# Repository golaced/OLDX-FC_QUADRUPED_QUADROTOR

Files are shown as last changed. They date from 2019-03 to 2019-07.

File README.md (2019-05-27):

# 1 OLDX-MocoMoco四足机器人开发平台项目  
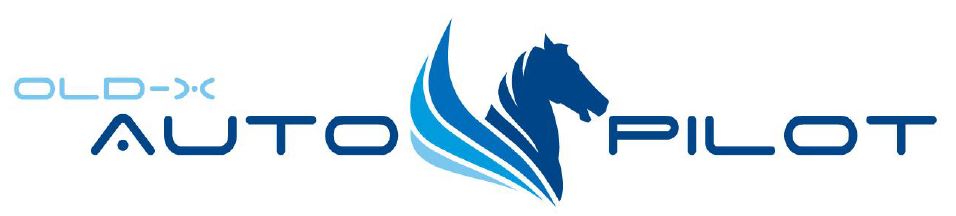
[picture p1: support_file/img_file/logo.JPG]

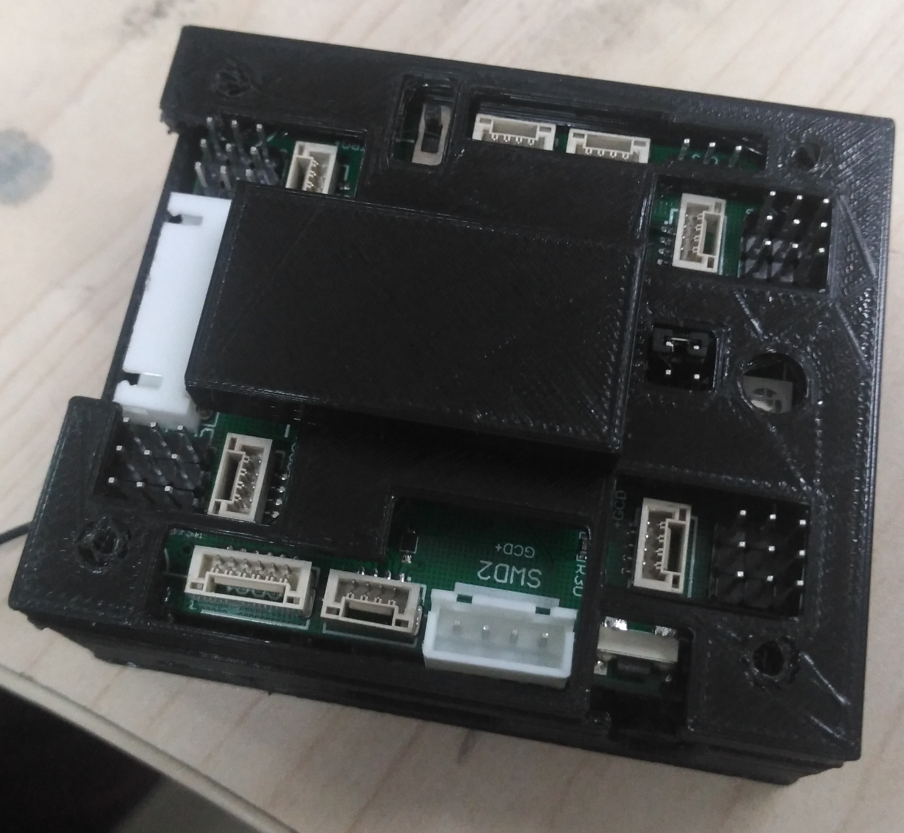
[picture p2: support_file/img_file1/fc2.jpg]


  ____OLDX-MocoMoco四足机器人（OLDX-MocoMoco Quadruped）是目前国内首个真正意义上的开源足式机器人二次开发平台，团队已经开发了一套完整的免费开源
  项目OLDX-FC，随着近年来波士顿动力公司不断推出的足式机器人引起了国内外许多爱好者的关注，也出现了许多电子发烧友自己开发的足式机器人，但
  不同于四轴飞行器仅采用无刷电机和机架就能进行开发，而足式机器人本身结构复杂特别是伺服驱动部分可以独立作为一个学科进行研究，因此造成了
  虽然有许多不错的足式机器人项目但是由于项目成本或者编程语言不为国内环境所熟悉的原因而阻碍了它们的推广或开源。团队4年前就开始研发的六
  足机器人具有丰富的机器人，通过将其与所开发的飞控项目二次结合推出了MocoMoco四足机器人开发平台，囊括机器人结构、步态算法和SLAM无人驾驶
  等多个足式机器人核心技术内容。项目遵循GPL协议，能对DEMO内相关源码进行修改和二次开发。<br><br>

**相关资料** 
机器人测试视频更新地址：https://www.bilibili.com/video/av46405055 <br>
为方便程序单独下载目前各版本固件从这下载：https://github.com/golaced/MocoMoco_Software<br>
机器人校准视频教程：https://www.bilibili.com/video/av51603154<br>
<br>
**-搭建该项目的方式-**

方式|说明|发货周期
-------------|-------------|-------------
整机购买(**推荐**)|从官方淘宝店购买碳素机架+已经加工好的控制器(不包含舵机)|最长半个月
机架打印+控制器购买|自行加工项目文件免费提供的3D打印机架 +从官方购买控制器+自己购买舵机|最长1周
机架打印+控制器制版加工|自行加工3D打印机架+自行制作、焊接控制器+自己购买舵机|控制器(4层板)+IMU+下载器转接+供电模块

**-开源程序与VMC机器人库-**

方式|说明|开源模式
-------------|-------------|-------------
(**VMC机器人库**)|支持多种着地反馈、动态步态调节和更稳定的姿态控制能力，需要向官方购买授权码|闭源(目前支持STM32F4系列，且库与芯片ID绑定)
开源程序|支持基础对角步态和姿态控制|开源

代码版本|开源代码说明|闭源VMC库说明
-------------|--------------|-------------
Publish Ver1.0|(1)虚拟模型基础步态<br>  (2)梯度下降姿态解算<br>  (3)NRF射频通讯遥控<br>  (4)UCOS操作系统|(1)虚拟模型+IMU自稳<br>  (2)动态步态+姿态调节
Publish Ver1.1|(1)SDK开发    |(1)SDK开发<br>	(2)自适应步频<br>	(3)平稳速度S函数切换
Publish Ver1.2|(1)梯度下降融合磁场+磁场干扰判断<br> (2)KF气压计高度融合<br>    (3)KF里程计位姿融合<br>    |(1)位置闭环控制+Jerk轨迹规划<br>   (2)跳跃API<br>   (3)SLIP模式<br> 	(4)梯度下降融合磁场+磁场干扰判断<br> (5)KF气压计高度融合<br>  (6)KF里程计位姿融合<br>   
		
官方机架taobao链接：https://item.taobao.com/item.htm?spm=a1z10.1-c.w4004-15110596499.22.6b86242c3mvjW9&id=589551490320
<br>
**-如果该项目对您有帮助请 Star 我们的项目-**<br>
**-如果您愿意分享对该项目的优化和改进请联系golaced@163.com或加入我们的QQ群567423074，加速开源项目的进度-**<br>

<br>
**-由于本人非专业研究四足机器人，该项目只是基于个人学术水平开发并不代表目前足式机器人算法就是这样，请不要过分依赖项目内容或与正规产品对比-**<br>
	
# 2 MocoMoco四足机器人平台介绍

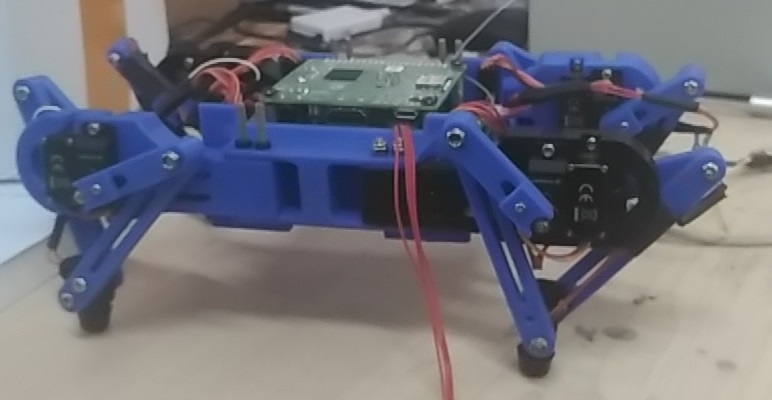
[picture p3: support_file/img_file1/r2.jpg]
 

____MocoMoco四足机器人是一个8自由度足式机器人其借鉴了GhostRobtic推出的Minitature机器人，之所以没有像波士顿动力或其他开发者一样采用
12自由度机器人是因为其在维护难度和成本上都大大提升，而8自由度机器人实际能完美的模拟12自由度单轴的控制特性能快速学习虚拟腿和
虚拟模型相关步态理论，仅损失了部分侧向移动能力。同时对小体积足式机器人来首先与自身移动速度其相比外部环境来说不存绝对意义上狭窄
的区域，能满足绝大部分室内外场景下的可靠移动。<br>
____另外驱动采用固定位置安装的方式使用寿命和维护难度都有较大的优势，适合实验调试中可能出现的损坏等情况。为降低伺服驱动成本将其采用的无刷电机替换为高性能舵机,采用碳板和3D打印件作为主体结构具有安装方便，容易维护的特点，是一个桌面级的四足机器人研发和SLAM算法验证平台。控制器方面采用了目前国内开发群体较多的STM32和树莓派，同时该硬件架构将在后续机器人项目中沿用将首先移植OLDX-FC飞控项目实现真正的
一板多用的目的。电路板硬件方面采用了一体化集成设计采用最小推出的树莓派A3+具有小体积高性能的特点能为后续图像、激光雷达SLAM提供开发可能，
控制板采用STM32F4作为处理器，板载3轴加速度计、3轴陀螺仪、3轴磁力计和气压计采用内减震设计，电路安装孔能完美与树莓派安装同时提供3D打印外壳。
控制板采用外部可更换供电模块供电具有12路PWM输出和4路AD采样，并外扩4路串口兼容正点原子推出的无线调试其方面机器人不同调试。

**控制器硬件参数：**

项目|参数
-------------|-------------
处理器|STM32F405RGT6
处理器性能|32Bit ARM Cortex-M4 168MH
陀螺仪 加速度计|LSM6DS33 
磁力计|LIS3MDL
气压计|MS5611
预留接口|GPS-1 串口-4 AD采样-4 着地开关输入-4
PWM 输出通道| 12通道输出 
供电|5V输入 舵机外部供电  AD传感器3.3/5V供电选择
图像处理器|树莓派A3+  1.4G 4核  带独立供电开关(控制板兼容树莓派全系列可作为外扩IO板安装，但通讯仅采用引脚串口)
遥控方式|2.4G射频 SBUS航模遥控
地面站|QGround   匿名地面站(需要额外OLDX-REMOTE监视器)

**机器人参数：**

项目|参数
-------------|-------------
足式机器人类型|8自由度并联机器人
尺寸|30cm * 20cm *10cm  
全腿长|8cm
重量|600g
供电|7.4V  18650 * 2(3000mah  续航>35 min) 带开关 
步态支持|Tort步态  Fly-Trot步态  波动步态
最大移动速度|0.4m/s
最大转向速度|30度/s
步态周期|>0.35 s
舵机性能|Kpower 12g金属舵机 *8(6V-60度/0.035s  9kg扭矩)
足底传感器|薄膜压力/微动开关(默认无传感器)
控制模式|遥控模式  姿态平衡模式(有/无着地传感器)  驾驶模式  

<br>
**控制器PCB接口说明：**
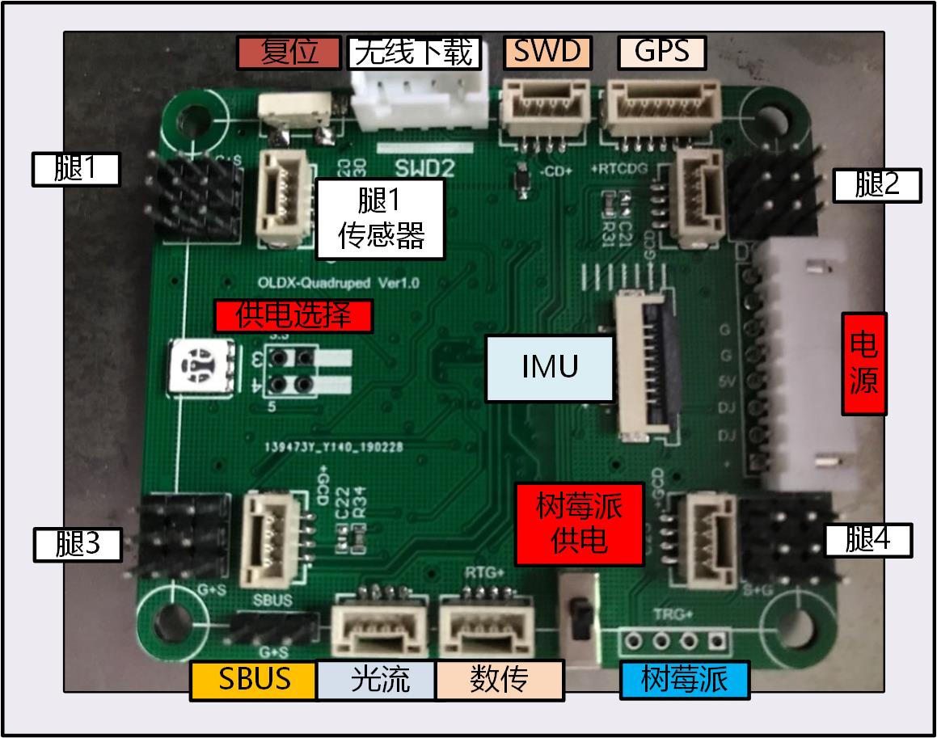
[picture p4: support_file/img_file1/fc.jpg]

<br>

接口|说明(以图片视角)|支持模块
-------------|-------------|-------------
复位|控制器复位按键|
无线下载|从左到右：GND SCK SWD 5V|接正点原子无线调试模块
SWD|从左到右：GND SWD SCK 5V|接Stlink 转接板
GPS|从左到右：5V RX2 TX2 SCL SDA GND|接MINIGPS
足底传感器|从上到下： VCC GND AD1/SCL1 KEY_GROUND1/SDA1|接压力/开关/震动/测距
供电选择|水平跳帽从上到下：3.3V  5V|
SBUS|从左到右：GND 5V Signal|天地飞接收机WBUS  Futaba SBUS接收机
光流|从左到右: RX4 TX4 GND 5V|接光流传感器
数传|从左到右: TX1 RX1 GND 5V|接匿名数传 
树莓派|从左到右：TX3 RX3 GND 5V|树莓派A3
腿1|从左到右：GND VCC PWM   从上到下：外侧舵机  里侧舵机  机械臂/云台|舵机外部供电
电源|从上到下：BEEP 舵机供电使能 GND GND 5V  VCC舵机  VCC舵机 VCC电池|电源模块 

**注：控制器机体为RGB LED方向，上表中仅给出腿1 舵机接口和传感器接口引脚顺序，其余三个腿为镜像对称的结构，
即以腿2为例 从上到下为：外侧舵机  内侧舵机  云台  从左到右为：PWM VCC GND    腿2传感器 从上到下为：
KEY_GROUND2/SDA2  AD2/SCL2  GND  VCC**

# 3 DEMO测试
____该项目免费提供了基础测试的3D打印机架能免费下载自行打印，官方将推出全碳版本的机架请
关注淘宝店后续推出的第三方扩展模块，控制器同时兼任二者各版本机架所需螺丝型号如下：

金属件|数量(3D打印机架)|装配
-------------|-------------|----------
M3*30|8|安装机臂
M2*10|8|安装舵机
M3*5|8|安装腿
M3*10|4|安装足底
M3*15铜柱|4|中心体支撑
M1.4*4|8|固定齿轮
M2.5*3|4|安装电池盒
M2.5*5|8|固定控制器
M2.5铜柱*4|4|控制器支撑

金属件|数量(官方碳素机架)|装配
-------------|-------------|----------
M2*16|8|固定机臂
M2*5|8|安装舵机
M3*5|8|安装腿
M3*10|4|安装足底
M3*32铜柱|4|中心体支撑
M3*4|8|中心体固定
M1.4*4|8|固定齿轮
M2.5*3|4|安装电池盒
M2.5*5|8|固定控制器

## 3.1 控制器组装（树莓派A3）
(1)安装树莓派：<br>
将树莓派按正确方向放入底部外壳中，为避免后续安装相机在该步骤时**最好将树莓派相机对应的CSI排线安装好**，将支撑柱子放入从底部用
M2.5将其与树莓派固定，将CSI排线从外壳对应槽中引出。
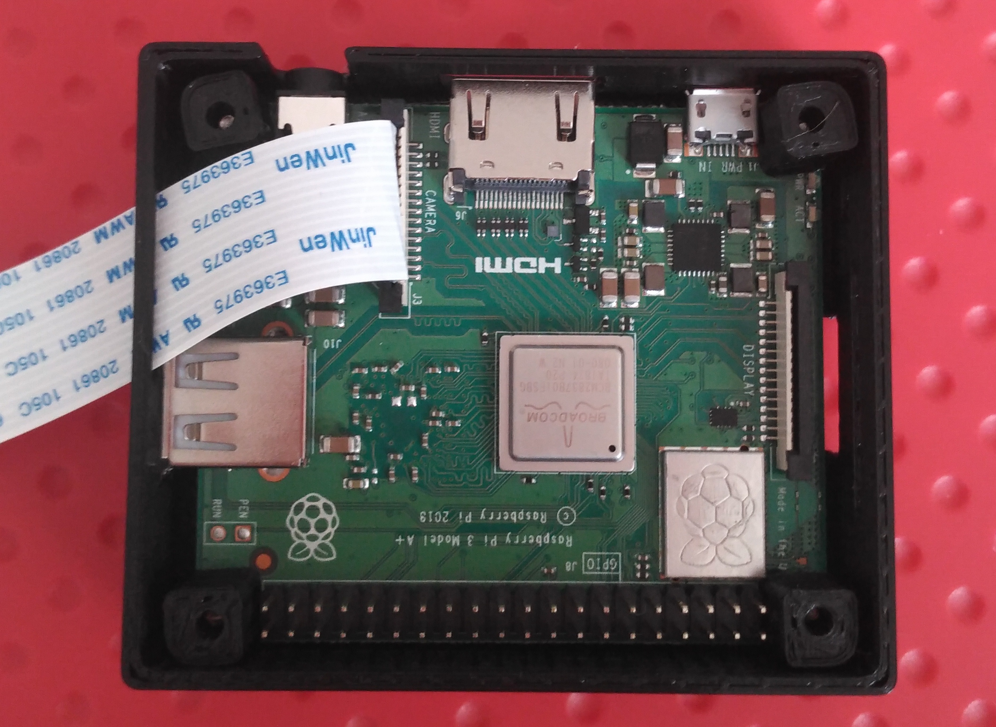
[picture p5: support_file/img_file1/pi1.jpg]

<br>

(2)安装控制器：<br>
将控制器NRF天线从底壳壁上对应圆孔引出，将其按正确朝向安装于树莓派上，注意控制板上只有4P母口其**顶头引脚并非对应树莓派顶头引脚**而且排针为外侧，正确安装应该如下图所示：
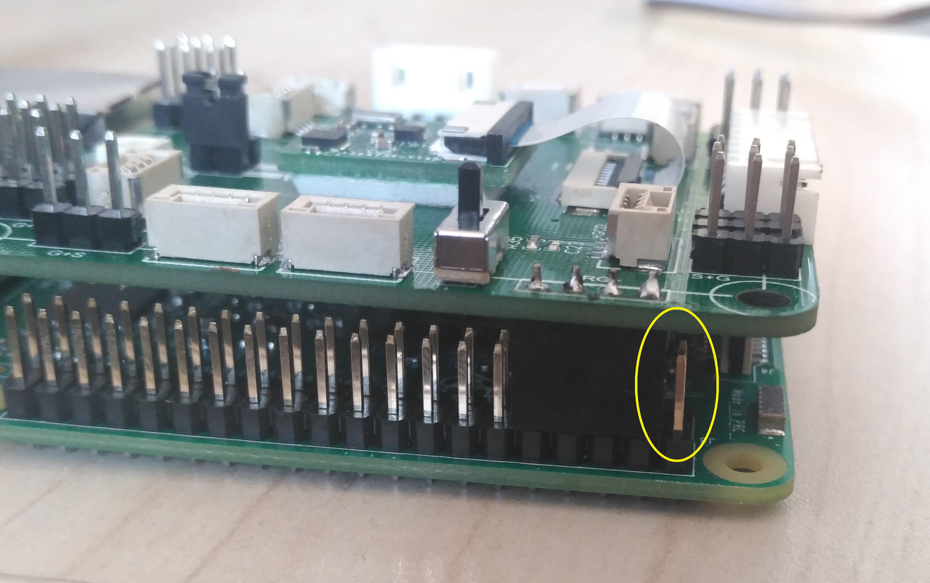
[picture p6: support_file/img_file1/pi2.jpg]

<br>

(3)安装上盖：<br>
将上壳以正确方向安装于控制板上，主要中心空槽应该完整包裹IMU板，完成后同样用M2.5螺丝将上盖固定完成控制器组装。
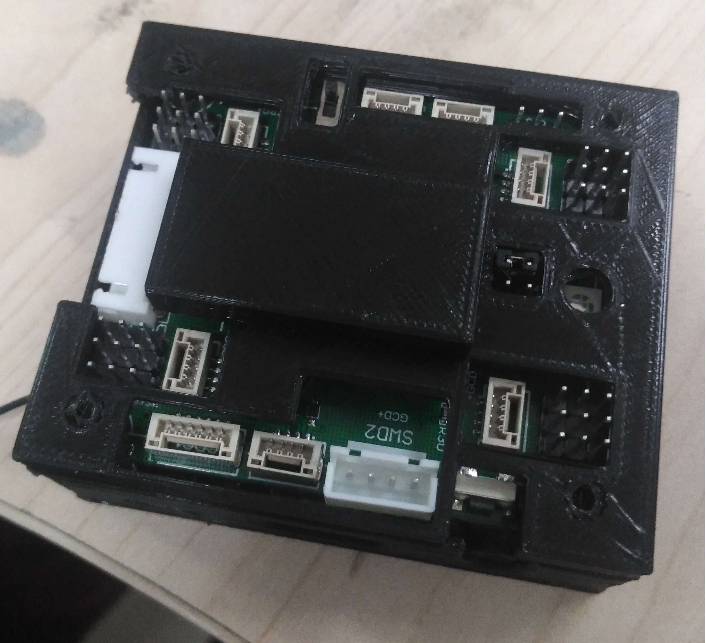
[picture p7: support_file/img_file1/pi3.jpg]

<br>

## 3.2 机器人组装（官方机架）
### 3.2.1 机臂和中心体组装
(1)组装机臂，需要2个机臂碳素片、半圆3D打印件、中心体3D打印支持件，注意机器人机臂需要具有5°的外扩角度，注意上板卡槽为L字，下板卡槽为T字，同时用2mm螺丝加固机臂，结果如下图所示：
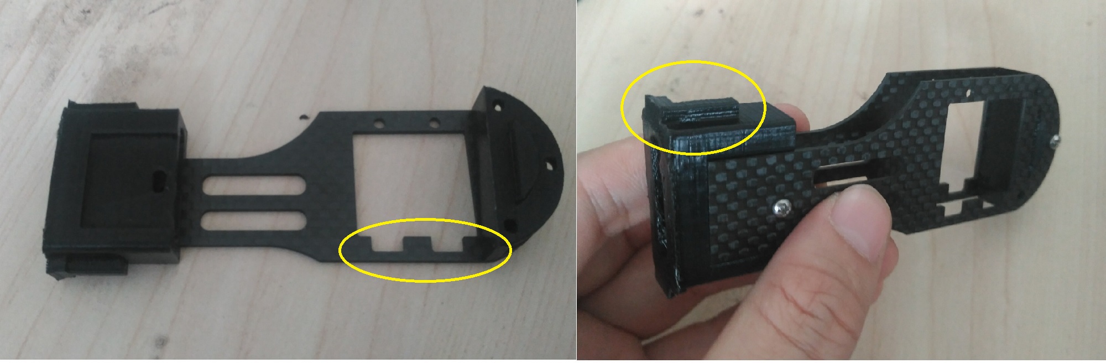
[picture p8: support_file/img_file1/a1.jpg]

<br>
(2)组装中心体，需要上下中心体碳素片、4个M3*32铜柱，首先将铜柱固定在底板上。
<br>
(3)安装机臂，将四个机臂固定在下板卡槽上注意要用5°外扩，结果如下图所示：
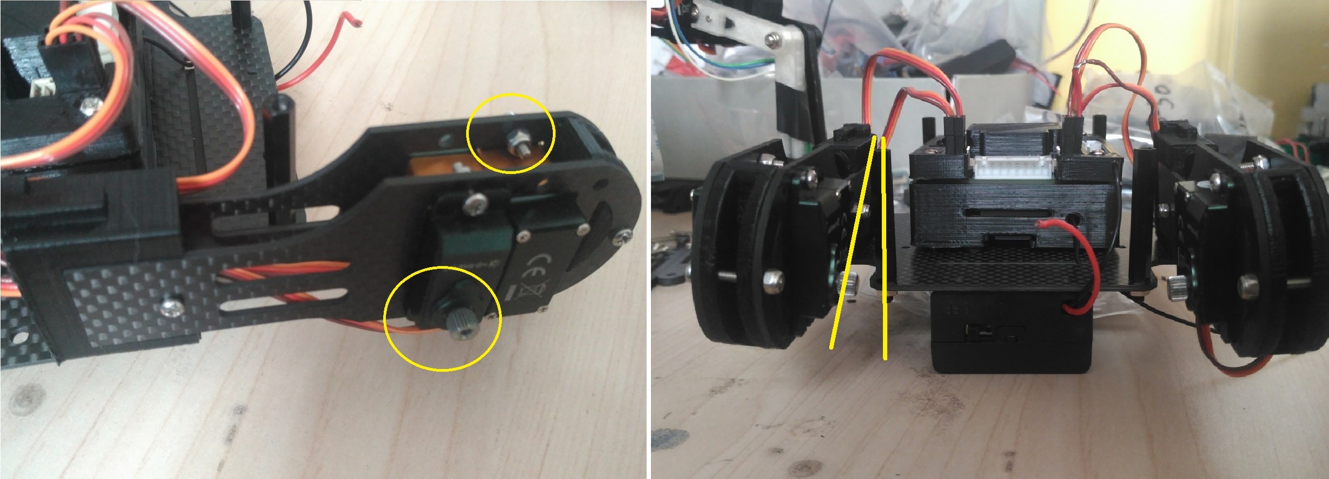
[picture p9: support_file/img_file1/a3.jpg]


### 3.2.2 安装电池仓、控制板和舵机
(1)首先安装电池仓，其安装在中心体底部并且开关方向朝向后方，结果如下图所示：
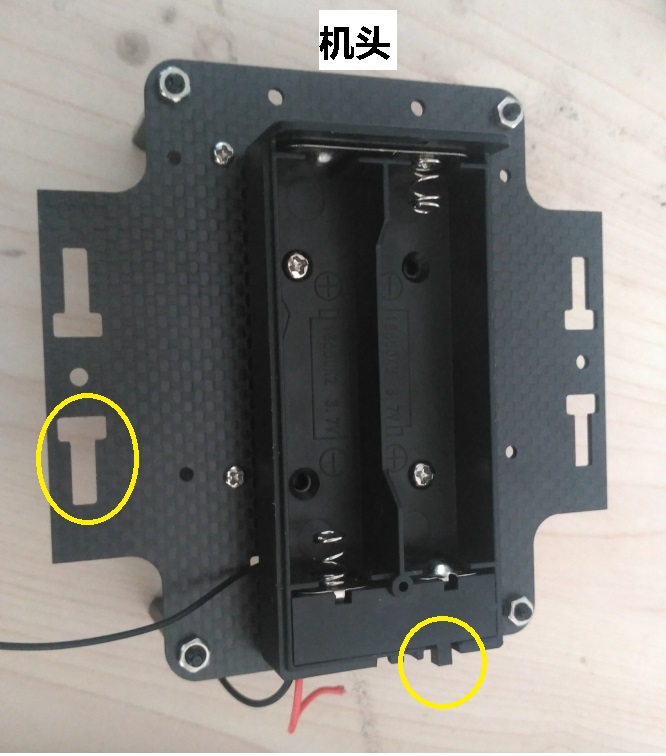
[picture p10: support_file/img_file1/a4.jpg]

<br>
(2)安装舵机，舵机安装采用轴承在下的方式,并且外侧舵机轴承朝向机体内部，内侧舵机轴承超外以保证腿部移动时不会受机体阻碍，用2mm自锁螺丝固定在碳板上，结果如下图所示:
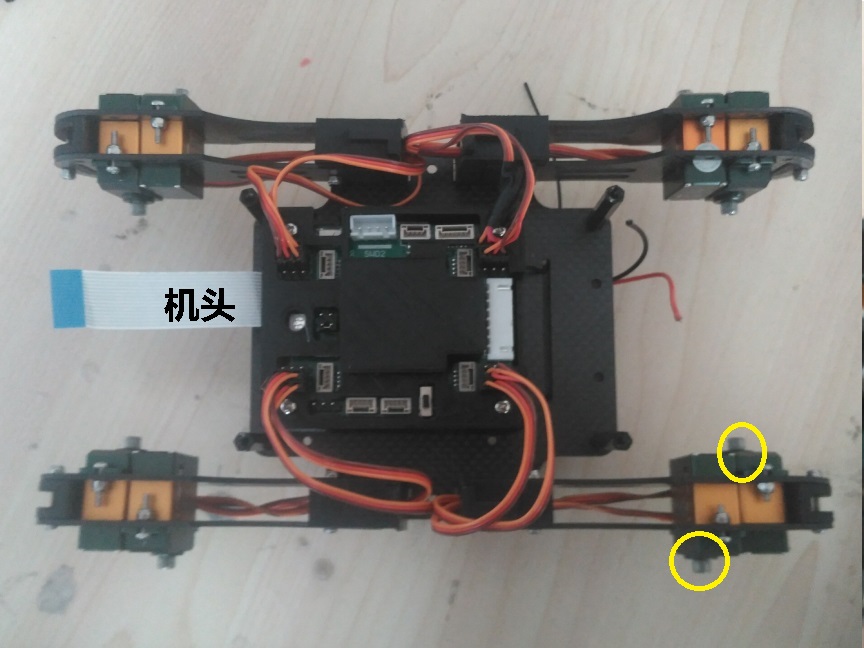
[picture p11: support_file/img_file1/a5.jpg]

<br>
(3)安装控制板，将控制板安装在中心体上方(**推荐用带锁3M胶或魔术贴方便后续SD卡更换**)，主要如没有安装控制器外壳则需要将控制器采用3D打印件垫高以防止电路板底部与碳板和电池仓估计螺丝短路，结果如下图所示:
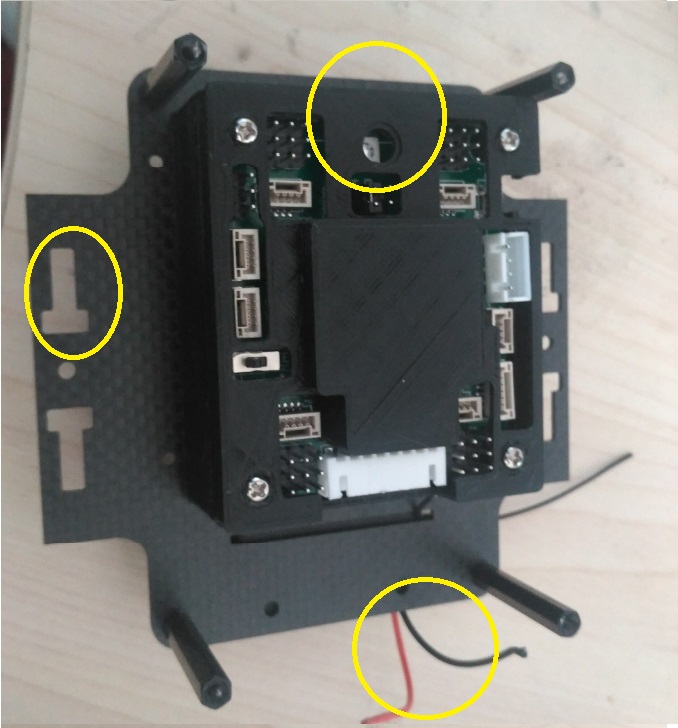
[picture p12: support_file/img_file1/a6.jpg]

<br>
(4)连接舵机线，从机臂内部绕线将舵机线与控制板连接，具体连接顺序参照下标，另外注意PWM引脚朝向机体内部为5V供电即可，具体引脚供电顺序参考PCB IO图：

**舵机接线**
||
-------------|-------------|----------
Sch.PWM3 TIM3_3 [D_LEG] 外舵机1|机体右 |Sch.PWM6 TIM4_2 [D_LEG] 外舵机2
Sch.PWM2 TIM3_2 [X_LEG] 内舵机1| |Sch.PWM5 TIM4_1 [X_LEG] 内舵机2
Sch.PWM1 TIM3_1 NS| |Sch.PWM4 TIM3_4 NS
**机头**||机尾
Sch.PWM7 TIM4_3 NS| |Sch.PWM10 TIM8_1 NS
Sch.PWM8 TIM4_4 [X_LEG] 内舵机3| |Sch.PWM11 TIM8_2 [X_LEG] 内舵机4
Sch.PWM9 TIM1_1 [D_LEG] 外舵机3|机体左 |PSch.WM12 TIM8_3 [D_LEG] 外舵机4

### 3.2.3 连接电子模块和上板
(1)将降压模块与电池仓焊接，注意输入输出关系和正负极，结果如下图所示:
<br>
(2)将降压模块通过XH2.8-8线进行连接，并将降压模块卡入底板后部卡槽，结果如下图所示:
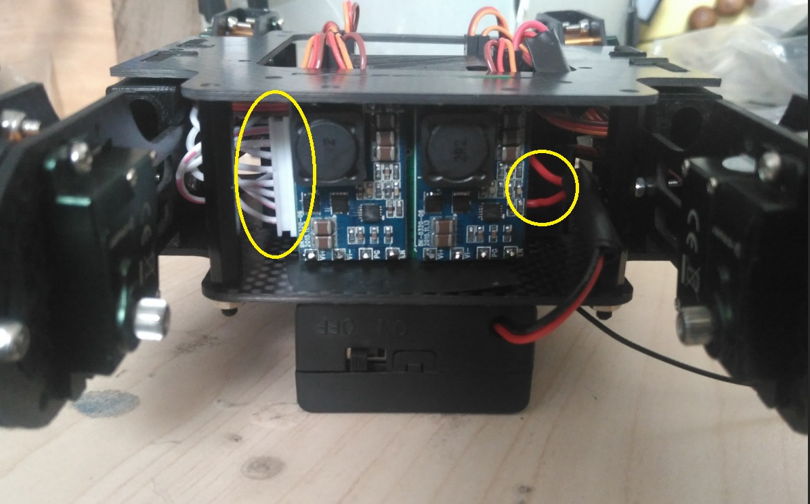
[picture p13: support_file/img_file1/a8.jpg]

<br>
(3)安装上板，将上板与降压模块和机臂卡槽对应安装，采用螺丝将上板与4个支撑铜柱固定，结果如下图所示：
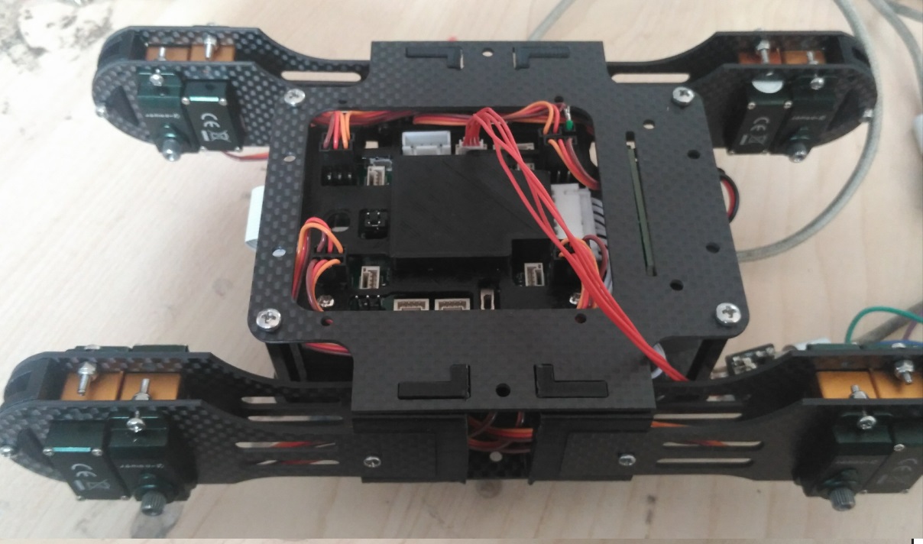
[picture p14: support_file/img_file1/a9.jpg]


## 3.3 腿部安装、偏差校准与IMU传感器校准（**十分重要**）
<br>**视频教程链接：https://www.bilibili.com/video/av47485521** <br>

**使用OLDX-Remoter快速校准**<br>

条件|说明
-------------|-------------
拨码1在右 其他在右 长按遥杆开关6s|提示音后校准加速度计和陀螺仪(需水平静置)
拨码1在左 其他在右 长按遥杆开关6s|黄灯常亮，蜂鸣器间断响起，360°各面旋转控制器12s完成磁力计校准
拨码1和2都在左 其他在右 上下竖直连续波动多次遥杆|提示音后进入舵机校准模式，舵机自动供电(需拆除腿部)，蜂鸣器以次数提示舵机编号，长扒遥杆左右改变舵机选择，上下微调舵机偏差

**注意！！！：由于IMU采用软线与控制板连接不牢固或被挤压下会出现SPI通讯错误，因此电路板正常工作时module.flash和module.nrf都为1且
控制器平放下mems中加速度原始值约为[0 0 4096]左右，如不正常请断电重新连接排线DEBUG确认。另外电路板上电后如果为PX4开机声则90%以上
几率是正常此时只需要检查mems传感器数据是否有错误跳动！！**

(1)组装腿部支持结构，首先不连接足底3D打印件以方便后续腿部偏差安装，将舵机附带的齿轮臂与3D打印件组装并采用1.25mm螺丝固定防止滑落，结果如下图所示:
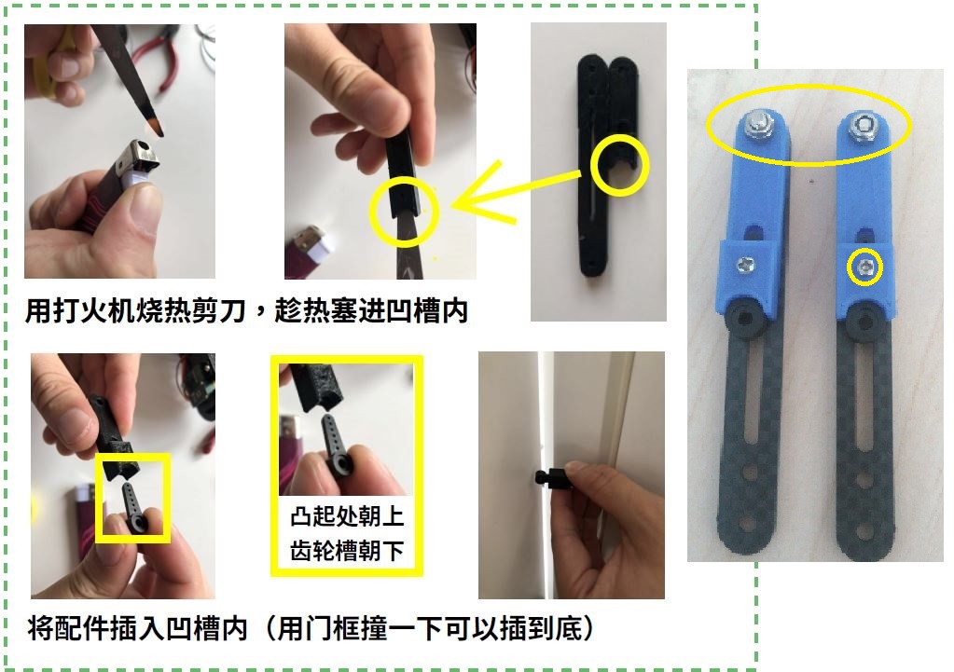
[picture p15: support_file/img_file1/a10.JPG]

<br>
(2)连接下载器对机器人供电测试系统供电是否正常，DEBUG程序对腿部结构偏差进行校准：（1.3以上固件已支持遥控器校准请参考word文档）<br>
a.首先将vmc_demo.c 文件下force_dj_off_reset加入watch中并在DEBUG中置为1将舵机偏差复位。<br>
b.将vmc_all.sita_test[4]置1此时舵机会被供电转动到默认偏差下的90°。<br>
c.将安装好的前后舵机摇臂以与机体保持水平的方式进行安装，如下图所示：
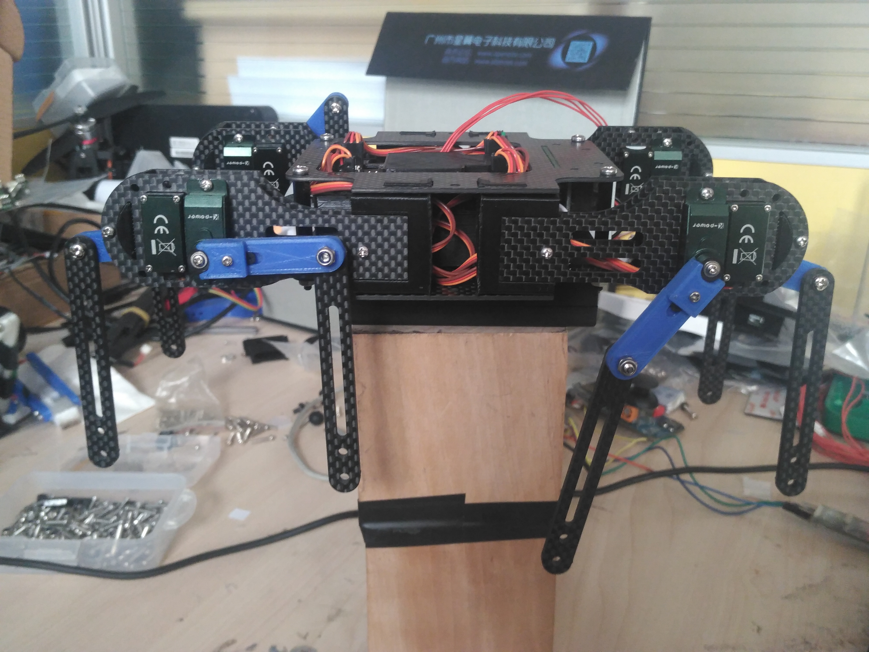
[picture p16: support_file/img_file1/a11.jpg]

d.修改vmc[i].param.PWM_OFF中的偏差参数，[0]对应外侧舵机角度[1]为内侧舵机通过调整参数和目视校准保证舵机90°绝对垂直，完成对4只角全部校准后用舵机配套螺丝固定轴承。<br>
e.将mems.Gyro_CALIBRATE置为1，将当前标定后的偏差存储在FLASH中。<br>
f.复位芯片查看读出的偏差是否一致。
<br>

(3)校准IMU传感器，将机器人以电池仓水平放置进行传感器零偏校准，将mems.Gyro_CALIBRATE和mems.Acc_CALIBRATE分别置为1完成陀螺仪和加速度计的校准。<br>
**注： 对加速度的标定会觉得姿态解算0°在哪，而如果存在偏差会导致机器人移动稳定性出现移动中向左或右偏离。因此在后续对一些
控制参数和舵机偏差标定进行FLASH保持时建议仅对mems.Gyro_CALIBRATE置1**
<br>

(4)安装足底3D打印件，如有足底传感器在控制板上连接对应传感器,如果没有则默认采用减震足底，将15*8mm的圆形软垫剪成半圆并排黏贴至底部，如下图所示：
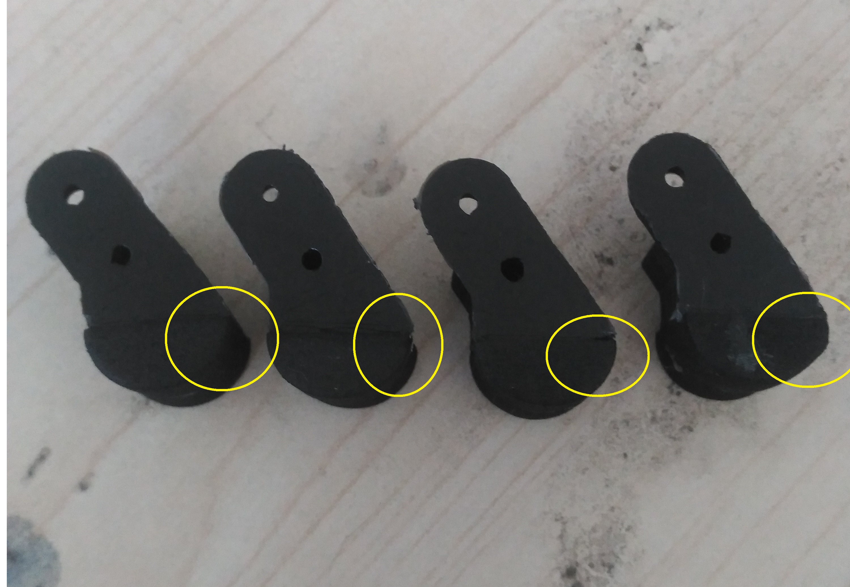
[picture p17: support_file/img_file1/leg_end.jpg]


**注意足底安装时4个足底的斜尖端都要朝向机头！！！**，最后完成整机的组装:
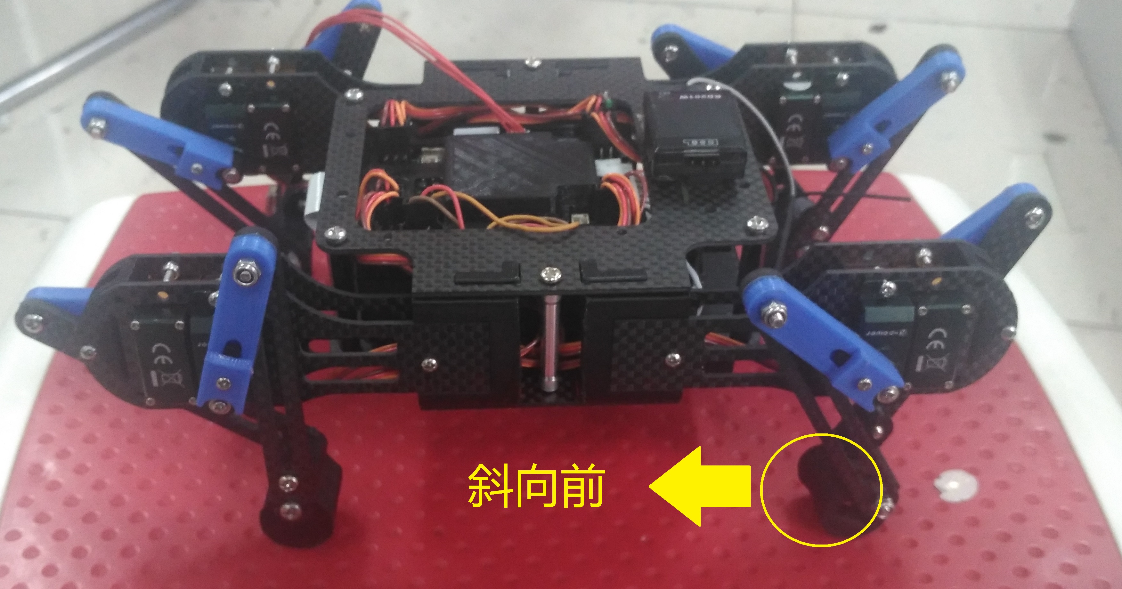
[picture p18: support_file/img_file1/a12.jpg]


## 3.4 手持遥控器(OLDX-Remote)介绍
____OLDX-Remote是OLDX机器人开发平台中一个通用的遥控器和数据监视器，其能兼容OLDX-FC飞控也能作为四足机器人的遥控器，
其除了能使用体感模式遥控机器人外，还能代替PC地面站进行实时参数调节，另外其实时回传SDK主状态机和子状态机运行状态，
期望高度速度信息和航线航点信息，能实时了解当前SDK运行状况和下一时刻飞行器的目标任务，解决了机器人自主控制中对其内部状态难以获取的问题。
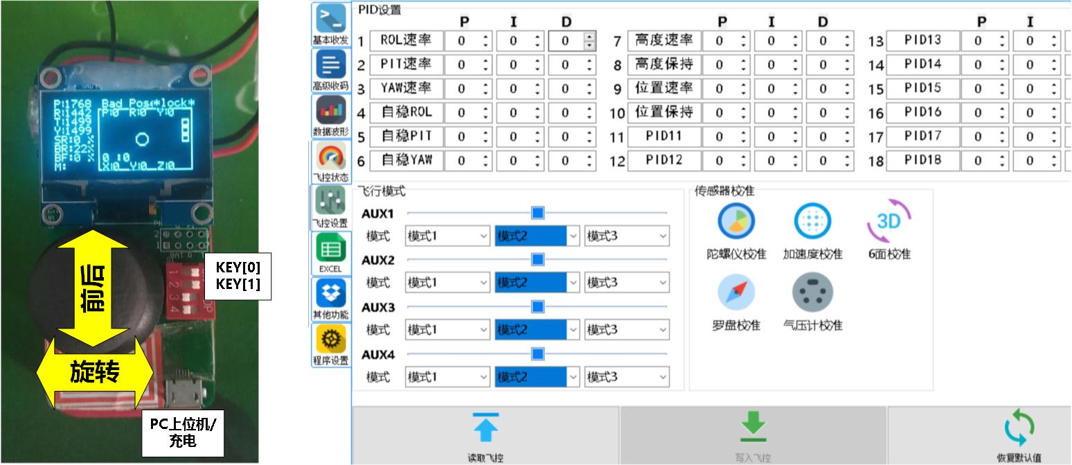
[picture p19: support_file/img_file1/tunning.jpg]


### 3.4.1 界面介绍
____OLDX-Remote开机后具有三类界面，（1）主界面：显示机器人高度，姿态，电压和时间等常用数据（2）PID参数界面与PC端地面站对应显示机器人内部参数（目前版本暂时无用）（3）
SDK界面：显示航线和自主任务命令，状态机状态。则各界面下英文缩写如下：

主界面|说明
-------------|-------------
P|OLDX-Remote 俯仰遥杆值(体感) 
R|OLDX-Remote 横滚遥杆值(体感)
T|OLDX-Remote 油门杆值(遥杆) **四足机器人前后控制**
Y|OLDX-Remote 航向杆值(遥杆) **四足机器人旋转控制**
SR|机器人与OLDX-Remote间的通信强度
BR|OLDX-Remote电量
BF|机器人电量(低电量时蜂鸣器会报警)
M|机器人模式 Mual->手动  
Bad Pos|定位模式状态  Bad Pos->无定位 GPS->卫星数量(推荐8颗以上起飞) Opt->光流质量
lock|机器人锁定情况
矩形界面中P|俯仰角
矩形界面中R|横滚角
矩形界面中Y|航向角
矩形界面中 0:0|时间
矩形界面中X,Y,Z|局部X轴位置(米)
矩形界面中 三个正方形点| 从上到下 *GPS连接  *图像设备连接 *光流模块连接
中心圆圈和实心点|巡线或视觉跟踪目标的像素位置

遥控器上有4个拨码开关其中**仅1和2号**有用，默认状态下对应程序中KEY[0]和KEY[1]，另外遥感下压触发按键对应KEY_SEL。拨码开关
在左为1右为0，默认程序中拨码开关对应功能如下：

拨码开关|说明
-------------|-------------
1号：左   2号：右|姿态俯仰Sin跟踪模式
1号：右   2号：左|车辆模式，前后给定位速度增量回中后保存当前速度
1号：左   2号：左|**强制断动力电**   用于舵机堵转保护，如无用直接关闭电池开关

<br><br>

PID参数界面（**待更新**）|说明
-------------|-------------
PIDX-X|上位机中对应参数
左右拨动遥感到底2s左右可切换界面|
左右上下选择PID参数|
点击遥控出现*则选中该参数|选中下左右增加100参数 上下增加10参数
选择下再次点击退出选中—|遥控器每5s读取飞控数据 选中下不读取 
选中中长按遥感遥控发出BB声则参数写入|对CHE遥控通道来说其写入 需到主界面进行相同操作 同时会校准遥控IMU

<br><br>

SDK界面（**待更新**）|说明
-------------|-------------
main|Idle(状态机默认状态 该状态自动起飞后才会运行SDK)  Mission(SDK模式)  Safe(状态机保护进入普通悬停模式  需降落上锁后复位所用遥控开关方可清除)
RC右方%|飞行器电量
Subs|子状态机状态
Way|剩余航点数量
左方竖条|高度期望和反馈  位置模式(期望为横线当前为矩形中心) 速度模式(显示上升下降期望速度)
矩形框|位置期望和反馈   中心为当前飞行器位置，原点为期望位置(坐标系为x-y  东-北)，坐标系尺度自动缩放，小横线表示飞行器机体方向
Dis|下一个航点距离(米)

## 3.5 移动测试
(1)平地测试<br>
____在平地上进行移动测试，以验证步态算法逻辑，前进和旋转速度控制以及其他导航轨迹控制。<br>

(2)前方上下台阶<br>
____从平地上一本书或多本书构成的台阶，以验证姿态控制和仿地跟随的能力。<br>

(3)左右侧上下台阶<br>
____从平地上一本书或多本书构成的台阶，保证仅左侧或右侧两条腿上台阶，以验证横滚轴姿态控制稳定性。<br>

(4)上斜坡高处下平台<br>
____从平地上15°~20°的斜坡，以验证步态对上坡抗打滑的能力，并直接从坡顶部直接下台阶以验证腿部突然不对称缩小下的不同调节能力。<br>

(5)平台姿态自稳<br>
____将机器人放置于一个可倾斜的平台，通过人为倾斜来验证姿态控制的可靠性。<br>

## 3.6 使用ST-link或正点原子无线下载器调试
____使用下载器转接板与控制板进行连接，需要4P双头卡槽线、USB转接小板和大板以及一根micro USB线，连接后结果如下：
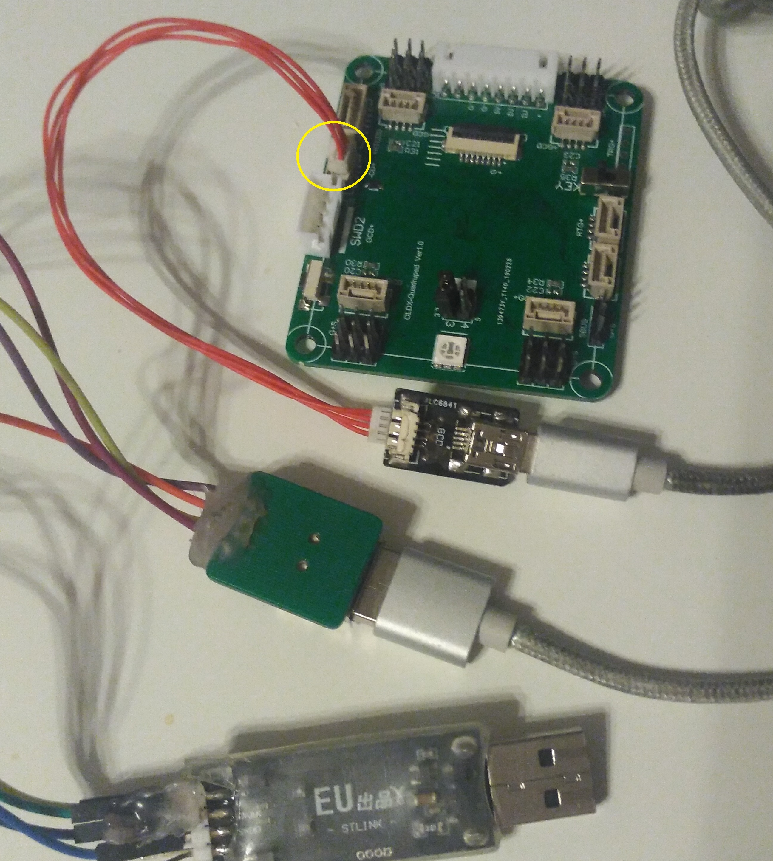
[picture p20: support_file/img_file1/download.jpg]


如采用正点原子无线下载器则请参考项目中附带的说明pdf文件，另外两种下载方式不可以同时使用。<br>

**注：KEIL5相关软件和芯片库下载：**<br>
```
链接：https://pan.baidu.com/s/1UNnMhOecPHUjdAQqanoYLQ 
提取码：az23 
```

## 3.7 高度和姿态Sin期望跟踪测试
____足式机器人基础稳定最重要的同样是基于IMU实现姿态自稳，通过在DEBUG模式下修改gait_test[i]能实现给定高度、俯仰角的Sin轨迹进行跟踪，
以验证控制器和参数的可靠性。通过在原地验证在再移动中验证可以看出不同步态算法的性能差距，在仅依靠舵机开环和无着地传感器前提下能实现的
最优步态效果如下：<br>
(1)不断跨腿下，机体高度能平滑变化<br>
(2)不断跨腿下，俯仰角能平滑变化<br>
(3)移动中同时实现上述过程<br>
(4)在可倾斜板子上验证姿态平衡，板子倾斜机器人快速反应保证机体平衡<br>

gait_test参数|说明
-------------|-------------
0|1高度______2俯仰角______3力矩测试
2|角度增量
3|幅值

**注：力矩测试是为了验证力矩闭环是否能够保证足尖跟踪给定曲线通过调节vmc_all.pid[Zr][P]/[D]适用不同驱动系统，另外修改UART_UP_LOAD_SEL=1
可在上位机上查看足尖期望反馈曲线**

## 3.8 参数调节
### 3.8.1 参数介绍
参数VMC_ALL|说明|默认值
-------------|-------------|-------------
end_sample_dt|足底速度微分时间间隔|0.01
ground_dump|腿触地瞬间回缩全腿长百分比|0.06
trig_ground_st_rate|跨腿时能触发传感器着地的时间百分比|0.63
ground_rst|自触地逻辑运行周期|0.06
k_auto_time|使能步态周期随姿态动态调节|0
trig_mode|跨腿轨迹模式|1
out_range_force|超出腿部空间时回缩力度|5
use_att|使用姿态控制|1
use_ground_sensor|使用着地传感器|0
l1|小腿长度|
l2|大腿长度|
H|机体长度|
W|机体宽度|
mess|机器人总体重量|
cog_off|F前进时重心偏差 B后退偏差  2前进俯仰角倾斜幅度 3转向横滚角倾斜幅度|
kp_touch|跨腿完成未着地下探增益|0.3
kp_trig|0 跨腿速度误差增益|0.125
pid[Xr]|前后速度误差PID|
pid[Zr]|Z轴足尖误差PID|
pid_att[YAWr]|航向控制PID|

### 3.8.2 上位机回传数据
____如果用户购买了远程监视器，则可以通过其上的虚拟USB串口连接PC机并通过匿名上位机实时参考机器人内部参数并绘制波形，加快参数调节
和步态算法的验证，通过设置UART_UP_LOAD_SEL可以实现不同参数上传的选择：

UART_UP_LOAD_SEL|说明
-------------|--------------
0|着地信号
1|足尖速度和反馈
2|激光测距结果
3|航向控制
4|横滚轴控制
5|机体加速度
6|足底压力值
7|压力与触地信号
8|高度失配

另外用户可自行在代码中发送函数同添加对应帧协议传输自己希望显示的数据：
```
ucos_task.c 256行
			case 用户定义:
			data_per_uart_rc(
			数据1，数据2，数据3，
			数据4，数据5，数据6，
			数据7，数据8，数据9，
			(int16_t)(0*10),(int16_t)(0*10.0),(int16_t)(0*10.0),0,0,0/10,0);break;
			default:break;
```		

**注意：**发送的为整数因此float参数需要扩大10的倍数才能正常显示！

## 3.9 DEMO程序优化和后续开发建议
____DEMO程序为用户提供了一个最简单和四足机器人开发框架，包括了姿态解算和核心步态算法。所提供的步态算法以虚拟模型为基础
通过雅克比矩阵输出扭矩，由于使用舵机因此仅通过简单的PD控制器变换为舵机旋转速度。在步态方面DEMO成像的整个状态机调度
结构与机器人库一样，只是简化了其中姿态控制策略采用了更简单直接的力控制方式，易于理解四足机器人最基础控制理论并能进一步进行
优化和改进。如果想深入对该项目进行开发并用于大型机器人中建议进一步研究SLIP模型、阻抗控制和柔顺控制理论，另外四足机器人
的核心有60%以上在可靠的伺服驱动，高效的伺服驱动系统能实现在最简单Sin轨迹+CPG算法下的可靠移动这一点已经被许多论文所
证明，机器人腿部结构设计也能在一定程度上提供自身稳定性。综上，后续升入开发建议如下：<br>
（1）优化腿部结构增加被动缓冲，构建12自由度机器人，增加着地传感器反馈<br>
（2）引入机器人倒立摆模型和基于模型先验知识下的优化控制、力矩控制<br>
（3）替换驱动系统采用无刷直驱或行星减速的结构提高各腿的一致性<br>
（4）引入视觉导航信息提高机器人移动的稳定性和足端轨迹的合理性

# 4 SDK开发
____该项目采用开源+机器人控制库授权的方式，即提供一个能运行机器人平台的基础项目源码同时提供高性能的闭源机器人控制库，
开源程序能进行修改和二次开发官方也会后续不断完善并与闭源机器人库一致。闭源机器人库则预留了完整的调用接口能基于SDK
快速地对机器人速度，姿态，足端轨迹，力矩等进行控制读取机器人位姿融合数据，即可采用现在SLAM小车底盘的开发方式对机器人进行
控制，二者具体功能区别如下：

**OLDX_VMC四足机器人数学库与开源DEMO版本的区别：**

项目|开源程序|闭源机器人库
-------------|--------------|-------------
步态算法|Trot|Fly-Tort  Tort  波动步态
步态理论|虚拟模型|虚拟模型
跨腿轨迹|摆线|最小Jerk轨迹  地面角度动态调节
足底传感器|无|压力  微动开关  震动传感器  距离传感器
图像导航|SDK开发|SDK开发
姿态控制|虚拟模型闭环|位置+虚拟模型闭环
速度闭环|机械参数估计|光流/视觉+机械参数估计
位置闭环|无|最小Jerk轨迹规划+ADRC轨迹跟踪
导航|光流  UWB  GPS|光流  UWB  GPS

## 4.1 获取授权库
____四足机器人数学库目前仅支持STM32F4系列单片机，数学库与单片机ID绑定一次性购买后则能永久使用且享受后续版本库的更新。
获取数学库前首先需要下载源码在watch中寻找并提供vmc_all.param.board_id对应的3个id。在向官方提供该ID并获取对应License
后修改源码中如下位置后即可正常使用否则在使用vmc.lib时不会为腿部进行供电和规划步态：

```
void vmc_init(void)
{ 	char i;
	get_license();
	//设置License
	vmc_all.param.your_key[0]=143;
	vmc_all.param.your_key[1]=42;
	vmc_all.param.your_key[2]=180;
```		

注：使用Demo程序需在vmc.h中定义#define USE_DEMO 1 否则默认使用数学库

## 4.2 步态测试
____采用VMC步态库时的测试方法与DEMO程序一样，同样可以进行Sin轨迹跟踪来测试步态性能的提升，另外更实际的方式是进行移动和
上下坡测试，用户可以通过使用步态数量高度的书本搭建楼梯、坡和障碍物，在桌面或室内完成步态算法的验证和测试，或者构建一个竞技场
与好友在后续图像自主控制中进行PK，如下图所示：

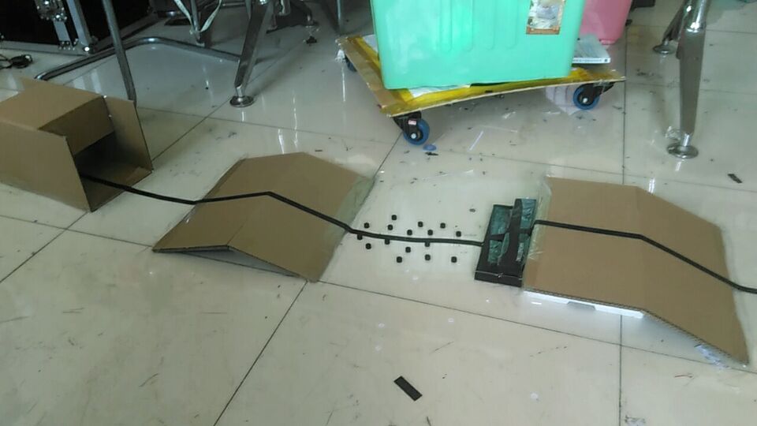
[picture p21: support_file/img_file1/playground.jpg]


## 4.3 参数调节

参数|说明|默认值
-------------|-------------|-------------
att_pid_all[PITr]|俯仰轴PID|i=8  d=0.001
att_pid_all[ROLr]|横滚轴PID|i=10  d=0.002
h_pid_all|高度PID|p=2  i=15  d=4

## 4.4 将控制器用于其他四足机器人
(1)足端轨迹输出<br> 
____如采用其他腿部构型的舵机驱动机器人可自行编程将vmc[i].epos转化为对应角度通过串口通信发送给用户的驱动控制器。<br>  
(2)力矩输出<br> 
____如采用相同构型的无刷驱动机器人则可将vmc[i].torque力矩作为输出通过通讯发送给伺服驱动,同时通过调节vmc_all.gain_torque来进行力矩单位的匹配。

## 4.5 SDK开发
____机器人开发采用ROS框架机器人控制器将作为一个硬件节点解算顶层控制命令，对机体中心点的姿态、速度和位置进行控制，同时也可以
对足端轨迹和力矩进行直接赋值。
<br>

set_body_spd|设置机体速度
-------------|-------------
x|前后速度
y|左右速度
z|上下速度  
完成条件|无

# 5 捐赠与项目后续开发计划
____团队计划后期推出5kg~10kg级的足式机器人开发底盘，支持RPlidar激光雷达导航进行SLAM算法验证，能以相同的价格替代目前市面上同类的四轮小车平台如Autolabor等。
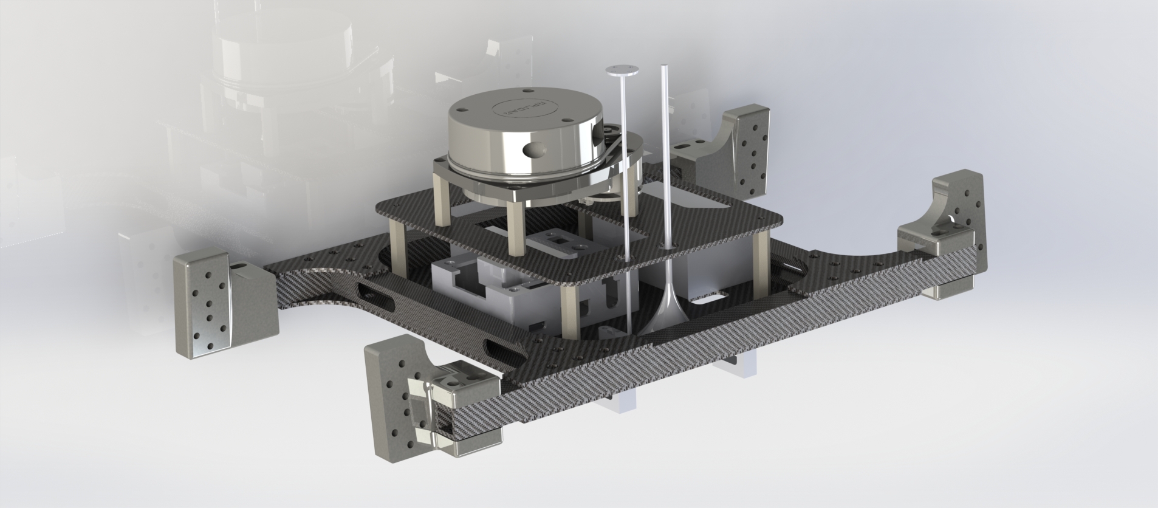
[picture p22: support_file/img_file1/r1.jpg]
 
____如果您觉得该项目对您有帮助，也为了更好的项目推进和软硬件更新，如果愿意请通过微信捐赠该项目！
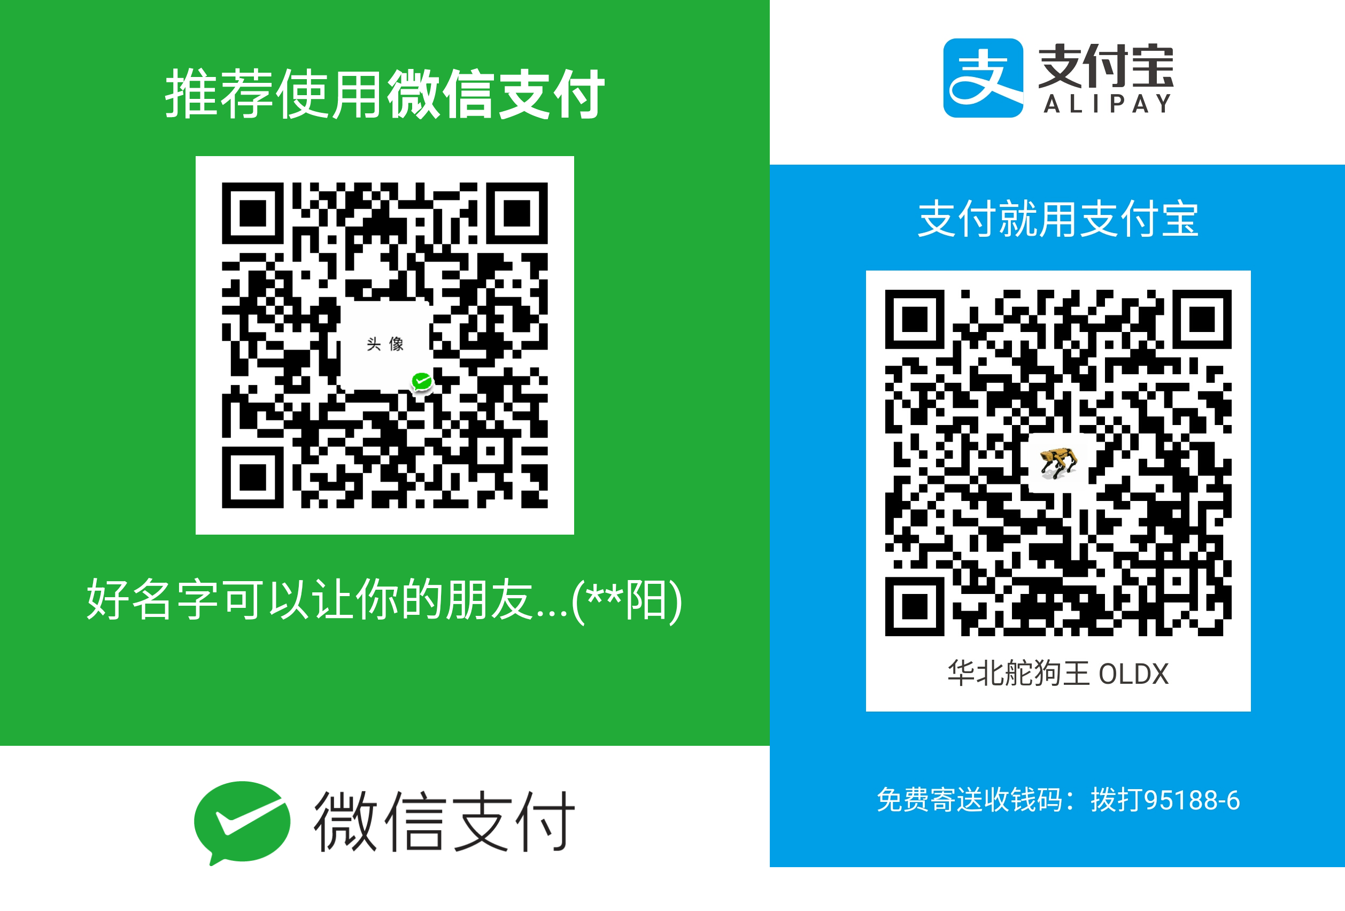
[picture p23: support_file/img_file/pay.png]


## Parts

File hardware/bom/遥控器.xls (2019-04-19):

Comment | Description | Designator | Footprint | Quantity
AS1364-BTDT-33 | 3.3稳压 | *U1 | TDFN-8 | 1
TP4059 | 充电芯片 | B1 | SOT23-6S | 1
1UF | 贴片电容 | C1, C3 | C0603 | 2
0.1UF | 贴片电容 | C2, C4, C5, C13, C14, C15, C16, C21, C47 | C0603 | 9
20PF | 贴片电容 | C6, C7 | C0603 | 2
10nf | 贴片电容 | C20, C23 | C0603 | 2
4.7uf | 贴片电容 | C22, C24 | C0603 | 2
22uF | 贴片电容 | C25 | C0603 | 1
10UF | 贴片电容 | C48 | C0603 | 1
BAT54WS | 单肖特基二极管 | D1 | SOD-323 | 1
IN4733 5.1V | 稳压二极管5.1V | D2 | 1n4148-SOD123 | 1
蜂鸣器 | 蜂鸣器 | DET1 | BEEP | 1 | https://item.taobao.com/item.htm?id=557399448031&ns=1&abbucket=8
方向摇杆 | 摇杆 | J1 | 摇杆2 | 1 | https://item.taobao.com/item.htm?id=531096275220&ns=1&abbucket=14 (https://item.taobao.com/item.htm?spm=a230r.1.14.99.30965b5bjNmqxk&id=531096275220&ns=1&abbucket=14)
DS0 | LED 蓝 | LED2 | LED_0603 | 1 | 遥杆需要配帽
MPU9250 | 传感器 | MPU1 | MPU_QFN24_0.4 | 1
Header 3 | 三段侧开关 | P2 | HDR1X3 | 1 | https://item.taobao.com/item.htm?id=526166466029
S8050 | 三极管 | Q1 | SOT-23R | 1
1K | 贴片电阻 | R1, R2, R10, R18, R19, R21, R52, R53 | R0603 | 8
1M | 贴片电阻 | R3 | R0603 | 1
10K | 贴片电阻 | R4, R5, R6, R7, R13, R14, R15, R16, R22 | R0603 | 9
10R | 贴片电阻 | R8, R9 | R0603 | 2
0R | 贴片电阻 | R11, R12 | R0603 | 2
4.7K | 贴片电阻 | R17, R20 | R0603 | 2
SW-DIP4 | 拨码开关 | S1 | DIP-8 | 1
SD | 自弹TF卡座 | SD_OLED1 | TF-MicroSD | 1
Header 4 | 卧贴侧端子 | SWD1 | JST_GH_V4 | 1 | 配2根4p双头线 | https://item.taobao.com/item.htm?spm=a1z09.2.0.0.51752e8dlo9hak&id=528691263571&_u=o1klsj894c50
STM32F103C8 | STM32F103c8 | U1 | LQFP48S | 1
USB-B(Mini) | USB | USB | Micro_USB | 1
8MHZ | 无源晶振 | X1 | PXCL | 1
NRF1 | NRF模组 | NRF1 | NRF | 1 | https://item.taobao.com/item.htm?spm=a1z09.2.0.0.65212e8dLKOq2l&id=45719116718&_u=31klsj89072b
OLED | OLED屏幕 | OLED | OLED | 1 | https://detail.tmall.com/item.htm?id=41844085048&spm=a1z09.2.0.0.51752e8dlo9hak&_u=o1klsj895f3e
供电端子(母) |  | https://item.taobao.com/item.htm?spm=a1z09.2.0.0.51752e8dlo9hak&id=39955787073&_u=o1klsj89d67d
G黑线

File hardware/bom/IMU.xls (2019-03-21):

Comment | Description | Designator | Footprint | LibRef | Quantity
0.1UF | Capacitor | C1 | C 0402 | CAP | 1
0.1UF | Capacitor | C2, C4, C6 | C0603 | CAP | 3
100nF | Capacitor | C3 | C0603 | CAP | 1
4.7uf | Capacitor | C5 | C0603 | CAP | 1
LIS3MDL | 磁力计 | LIS1 | LIS3MDL | LIS3MDL | 1 | 可选
LSM6DS33 | 加速度计 | LSM1 | LSM6DS33 | LSM6DS33 | 1
Header 8 | 8P 下接 抽屉 | MEMS1 | FH12-8S-1.0SH | Header 8 | 1 | 配1mm 8p软排线 异面 3 cm长
MS5611 | Sensor | MS1 | MS5611 | MS5611 | 1 | 可选

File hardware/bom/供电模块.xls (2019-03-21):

Comment | Description | Designator | Footprint | LibRef | Quantity
BAT54WS | 单肖特基二极管 | D1 | SOD-323 | BAT54 | 1
Header 8 | XH2.54 弯端子 | DC1 | HDR1X8 | Header 8 | 1 | 配8P双头线 | 6cm
DET402_1 | 蜂鸣器 | DET1 | BEEP | DET402_1 | 1
DCDC1 | 2.54排针 | DJ1, FC1 | DCDC1 | DCDC1 | 2
S8050 | 8050/BCW846/BCW847 | Q1, Q2 | SOT-23R | NPN | 2
1K | 0603 | R1, R4 | R0603 | Res2 | 2
10K | 0603 | R2 | R0603 | Res2 | 2
NC | 0603 | R3, R5 | R0805 | Res2 | 1
FC1 | 降压模块5V | 控制器供电 |  |  | 1 | https://item.taobao.com/item.htm?spm=a1z09.2.0.0.15212e8dszODOn&id=572382517694&_u=k1klsj89d0b4
DJ1 | 降压模块6V | 舵机供电 |  |  | 1 | https://item.taobao.com/item.htm?spm=a1z09.2.0.0.15212e8dszODOn&id=572382517694&_u=k1klsj89d0b4

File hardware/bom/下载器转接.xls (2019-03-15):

Comment | Description | Designator | Footprint | Quantity
0.1UF | Capacitor | C1 | C0603 | 1
1N4148 | 二极管 | D1 | 1n4148-SOD123 | 1
10K | 0603 | R1, R2 | R0603 | 2
MicroUSB口 |  | ST_Link_1 | USB/SM0.8-6H5_M | 1
4P卧贴 | Header, 4-Pin | SWD1 | JST_GH_V4 | 1 | https://item.taobao.com/item.htm?spm=a1z09.2.0.0.MJL2ZN&id=528744124006&_u=o1klsj899edd

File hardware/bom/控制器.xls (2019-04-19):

Comment | Description | Designator | Footprint | Quantity
AS1364-BTDT-33 | 降压模块 | *U1 | TDFN-8 | 1
0.1UF | 贴片电容 | C1, C9, C13, C15, C16, C17, C18 | C 0402 | 7
1UF | 贴片电容 | C2 | C 0402 | 1
2.2UF | 贴片电容 | C3, C4 | C0603 | 2
10NF | 贴片电容 | C5 | C 0402 | 1
20PF | 贴片电容 | C6, C7 | C 0402 | 2
4.7uf | 贴片电容 | C10, C12 | C0603 | 2
10nf | 贴片电容 | C11 | C0603 | 1
100uF | 贴片电容 | C19 | C0603 | 1
NC | 贴片电容 | C20, C21, C22, C23 | C0603 | 4
R0 | 单肖特基二极管 | D4 | SOD-323 | 1
SWD2 | 2.54 XH端子 4P 立贴 | SWD2 | SWD2 | 1
Header 8 | 2.54 XH端子 卧贴 | DC | HDR1X8 | 1
Header 4 | GH1.25端子 立贴 | FLOW, IIC1, IIC2, IIC3, IIC4, RADIO, SWD1 | JST_GH_V4 | 7
Header 6 | GH1.25端子 立贴 | GPS1 | JST_GH_V6 | 1 | https://item.taobao.com/item.htm?spm=a1z09.2.0.0.70a52e8drw8IxJ&id=528744124006&_u=l1klsj89de6f
MSK-12D19 | 立三档开关 | KEY | HDR1X3 | 1
5050 RGB | 三色LED | LEDRGB1 | 5050RGB | 1
Header 8 | 1mm软线 翻盖 下接 | MEMS | FH12-8S-1.0SH | 1 | 配30mm异面排线 | 配天线https://item.taobao.com/item.htm?spm=a1z09.2.0.0.16032e8daiTpOp&id=524223974321&_u=k1klsj898d21
NRF模组 | NRF模组 | NRF1 | NRF | 1 | https://item.taobao.com/item.htm?spm=a1z09.2.0.0.65212e8dLKOq2l&id=45719116718&_u=31klsj89072b
Header 3 | 2.54排针 | P1, P2, P3, P5, P6, P7, P8, P9, P10, P11, P12, P13, P14 | HDR1X3 | 13 | 向下焊接
Header 4 | 2.54排针母座 | PI1 | HDR1X4 | 1
S8050 | 8050/BCW846/BCW847 | Q2, Q3, Q4, Q5 | SOT-23R | 4
10K | 贴片电阻 | R1, R4, R5, R6, R33 | R 0402 | 5
1K | 贴片电阻 | R7, R11, R12, R30, R31, R34, R35 | R0603 | 7
560R | 贴片电阻 | R8, R10, R13, R17, R18, R19, R25, R26, R27, R28, R29, R32, R36 | R 0402 | 13
10K | 贴片电阻 | R9 | R0603 | 1
100R | 贴片电阻 | R14, R15, R16 | R 0402 | 3
1K | 贴片电阻 | R20, R21, R22 | R 0402 | 3
Header 2X2 | 2.54排针 | SEL | HDR2X2 | 1 | 配跳线帽
SW-PB1 | 侧贴按键 | SW1 | KEY_SAD | 1
STM32F405RGT6 | 单片机 | U1 | LQFP64_M | 1
W25X16 | W25X16;SST25VF016;MX25L1605 | U2 | W25Q32FVZPIG | 1
8MHZ | 无源晶振 | X1 | PXCL | 1
 | 图中LED焊接错误 缺口应在箭头处

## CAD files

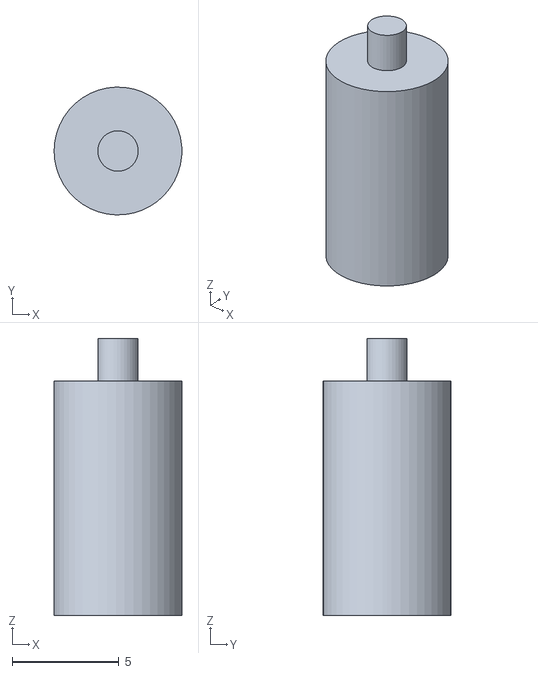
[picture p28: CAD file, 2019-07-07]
hardware/3D print/树莓派支撑_新.STL
6.00 x 6.00 x 13.0

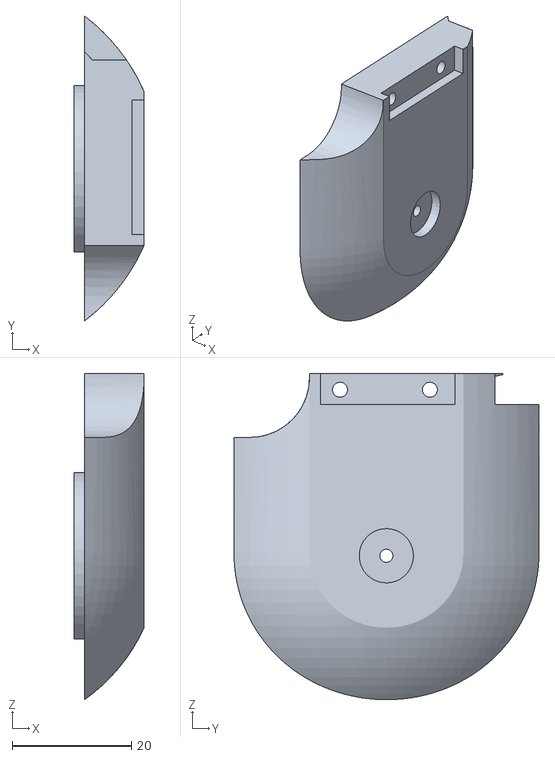
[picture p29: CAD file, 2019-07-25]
quadruped/3D打印测试机架/两轴云台2.STL
11.8 x 51.2 x 54.8

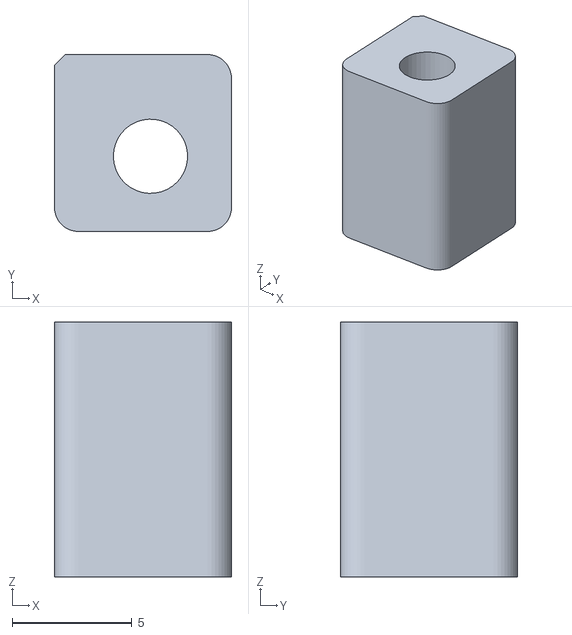
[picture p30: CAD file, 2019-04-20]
hardware/3D print/树莓派支撑.STL
7.39 x 7.39 x 10.6

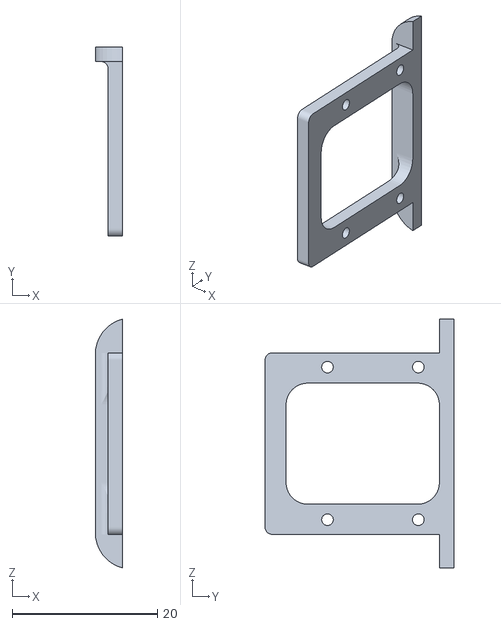
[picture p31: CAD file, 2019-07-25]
quadruped/3D打印测试机架/两轴云台5.STL
3.78 x 26.0 x 34.3

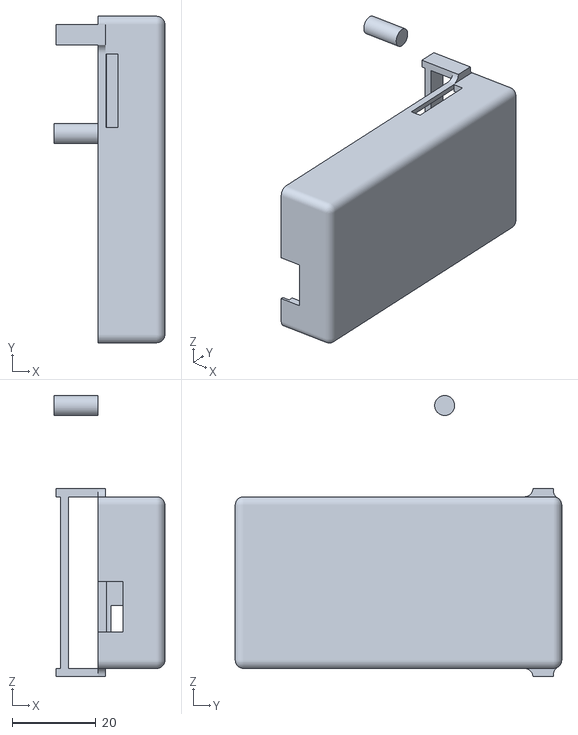
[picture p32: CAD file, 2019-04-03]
hardware/3D print/遥控器外壳.STL
26.5 x 78.0 x 67.1

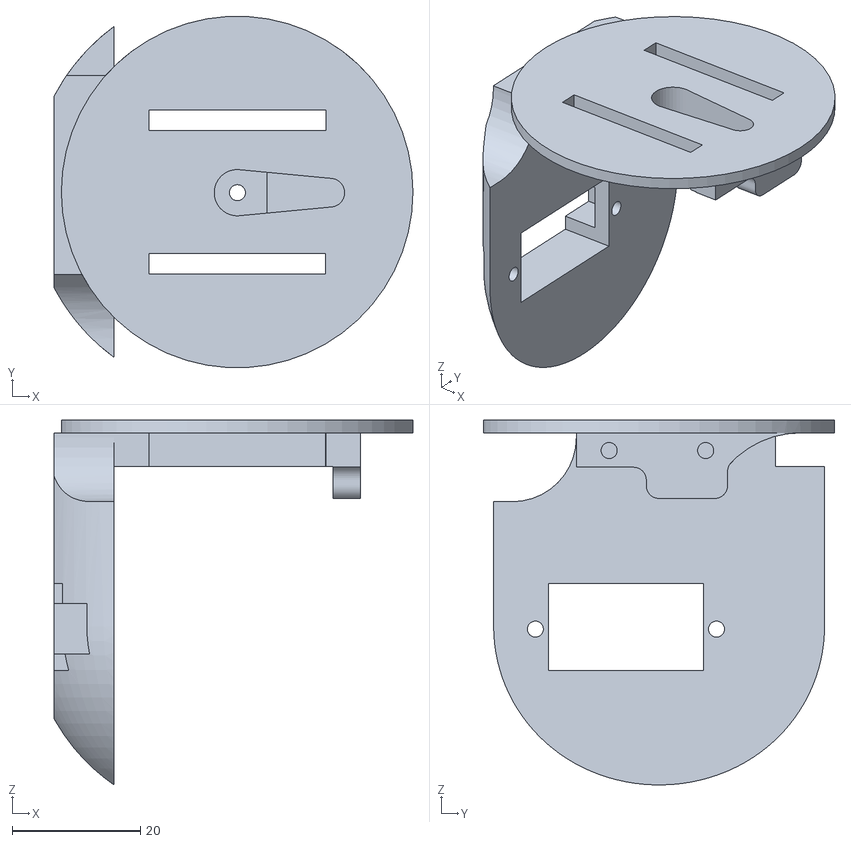
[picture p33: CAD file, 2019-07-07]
quadruped/3D打印测试机架/两轴云台3.STL
56.1 x 54.8 x 57.0

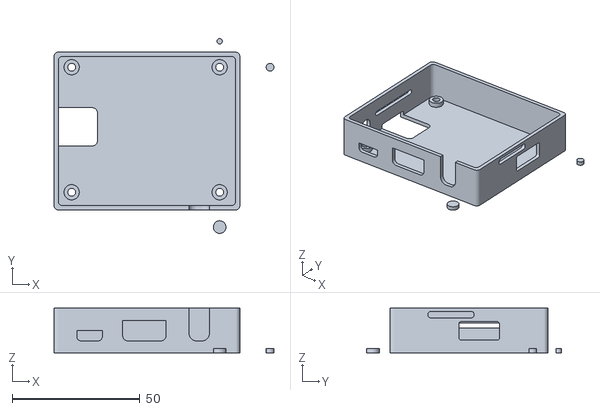
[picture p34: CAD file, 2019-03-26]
hardware/3D print/控制器外盒底.STL
86.2 x 76.4 x 17.5

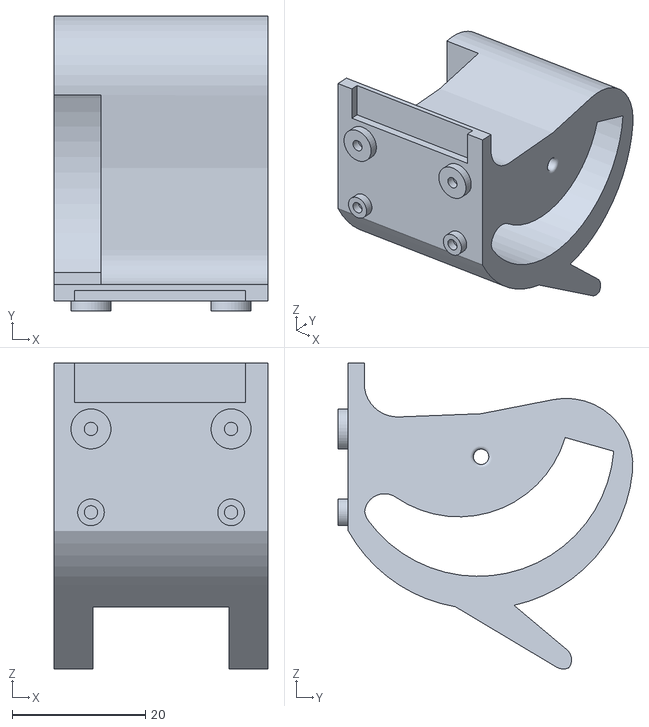
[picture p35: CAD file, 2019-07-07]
quadruped/3D打印测试机架/两轴云台1.STL
32.0 x 44.1 x 45.9

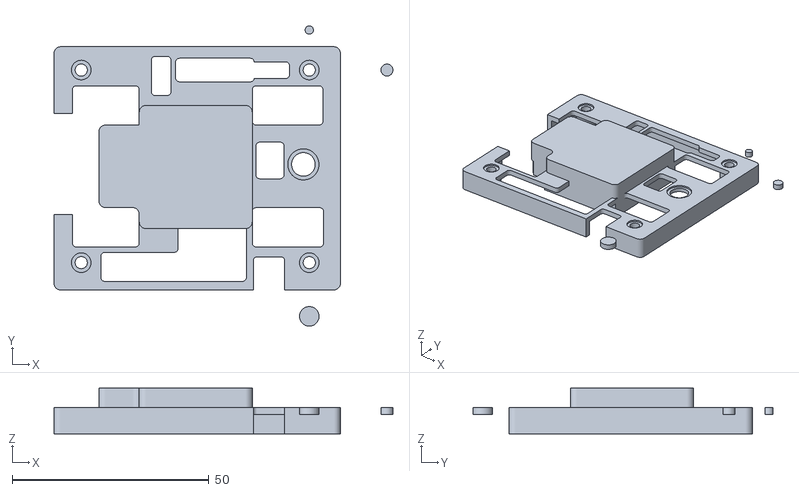
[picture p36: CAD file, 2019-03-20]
hardware/3D print/控制器外壳顶.STL
86.2 x 76.4 x 11.7

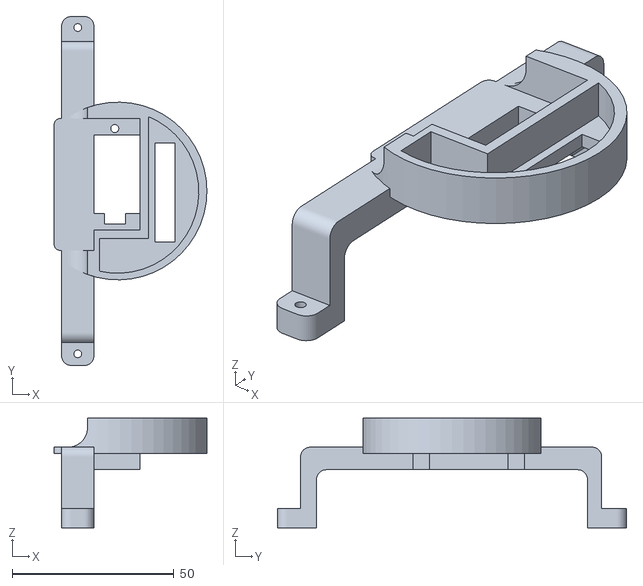
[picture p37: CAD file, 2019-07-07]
quadruped/3D打印测试机架/两轴云台4.STL
47.3 x 108.0 x 34.0

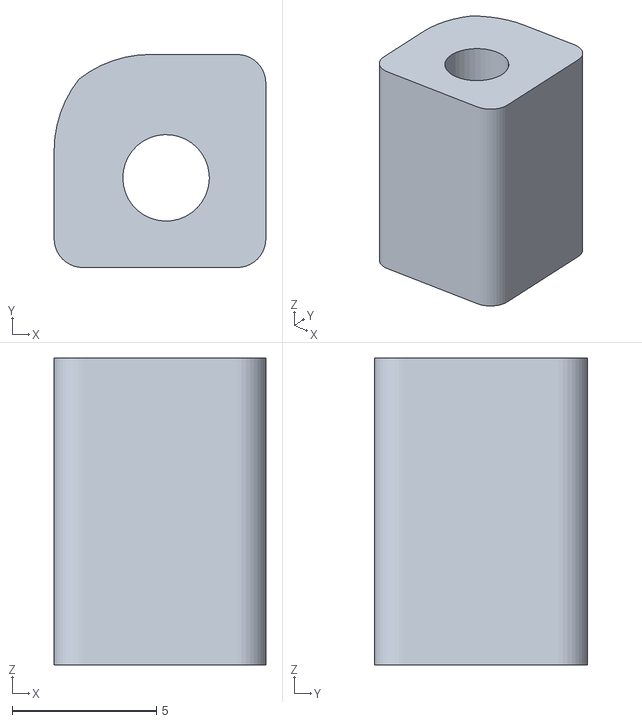
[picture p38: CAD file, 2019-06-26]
quadruped/3D打印测试机架/控制器外壳支撑.STL
7.35 x 7.39 x 10.6

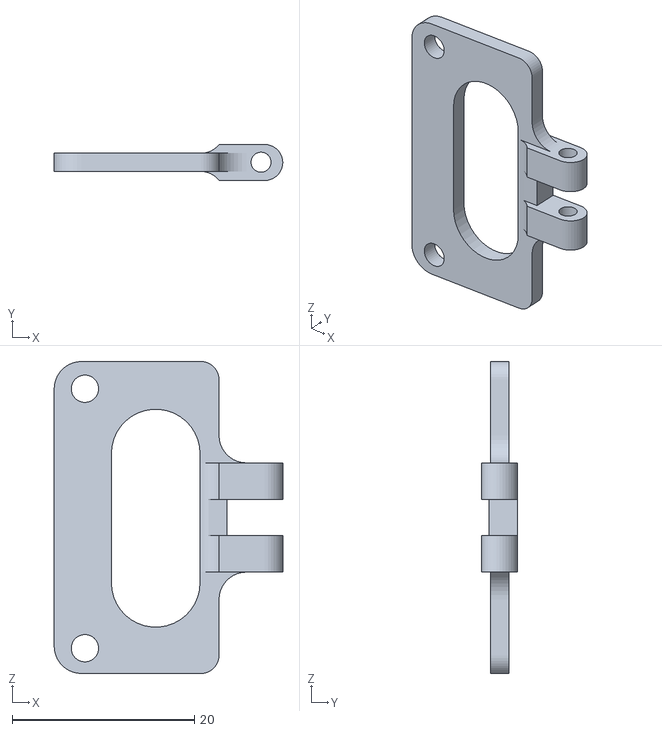
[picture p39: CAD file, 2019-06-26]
quadruped/3D打印测试机架/相机支撑可调 2.STL
25.1 x 3.96 x 34.3

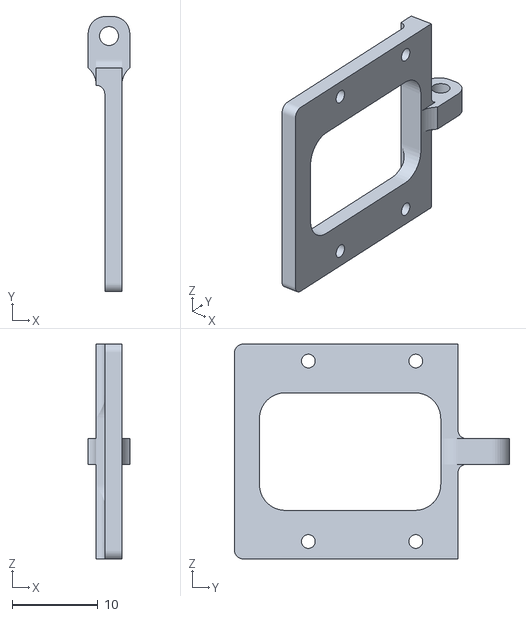
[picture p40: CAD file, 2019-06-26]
quadruped/3D打印测试机架/相机支撑可调1.STL
4.85 x 32.0 x 25.0

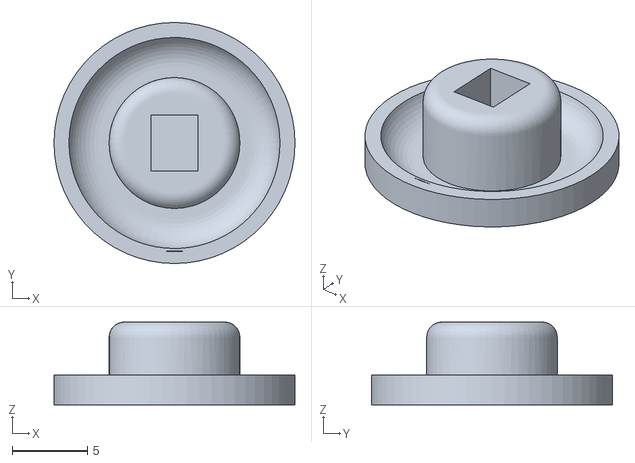
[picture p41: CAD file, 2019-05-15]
quadruped/3D打印测试机架/足底带传感器1.STL
16.0 x 16.0 x 5.50

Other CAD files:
quadruped/3D打印测试机架/足底带传感器2(需镜像打印).STL
quadruped/3D打印测试机架/树莓派相机支撑.STL
quadruped/3D打印测试机架/足底可加缓冲(需镜像打印).STL
quadruped/3D打印测试机架/机臂.STL
quadruped/3D打印测试机架/中心体.STL
quadruped/3D打印测试机架/腿关节.STL
quadruped/3D打印测试机架/腿舵机连接关节.STL
quadruped/3D打印测试机架/足底无缓冲.STL

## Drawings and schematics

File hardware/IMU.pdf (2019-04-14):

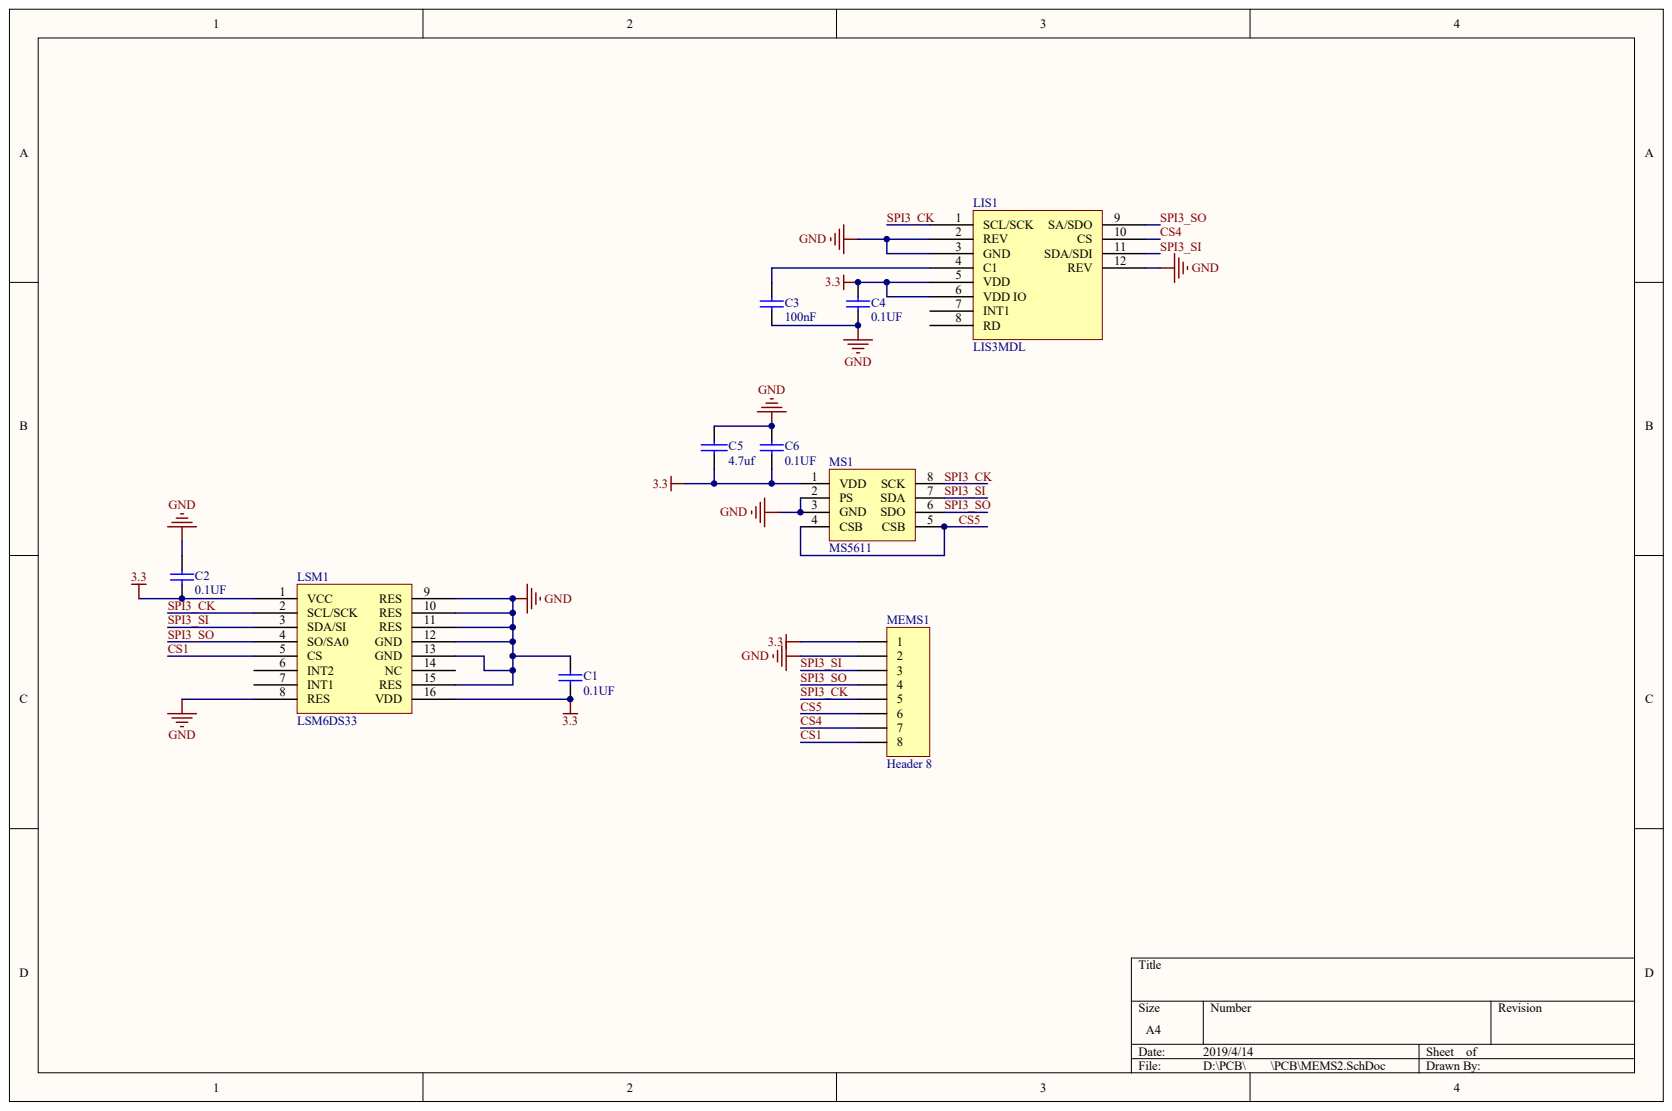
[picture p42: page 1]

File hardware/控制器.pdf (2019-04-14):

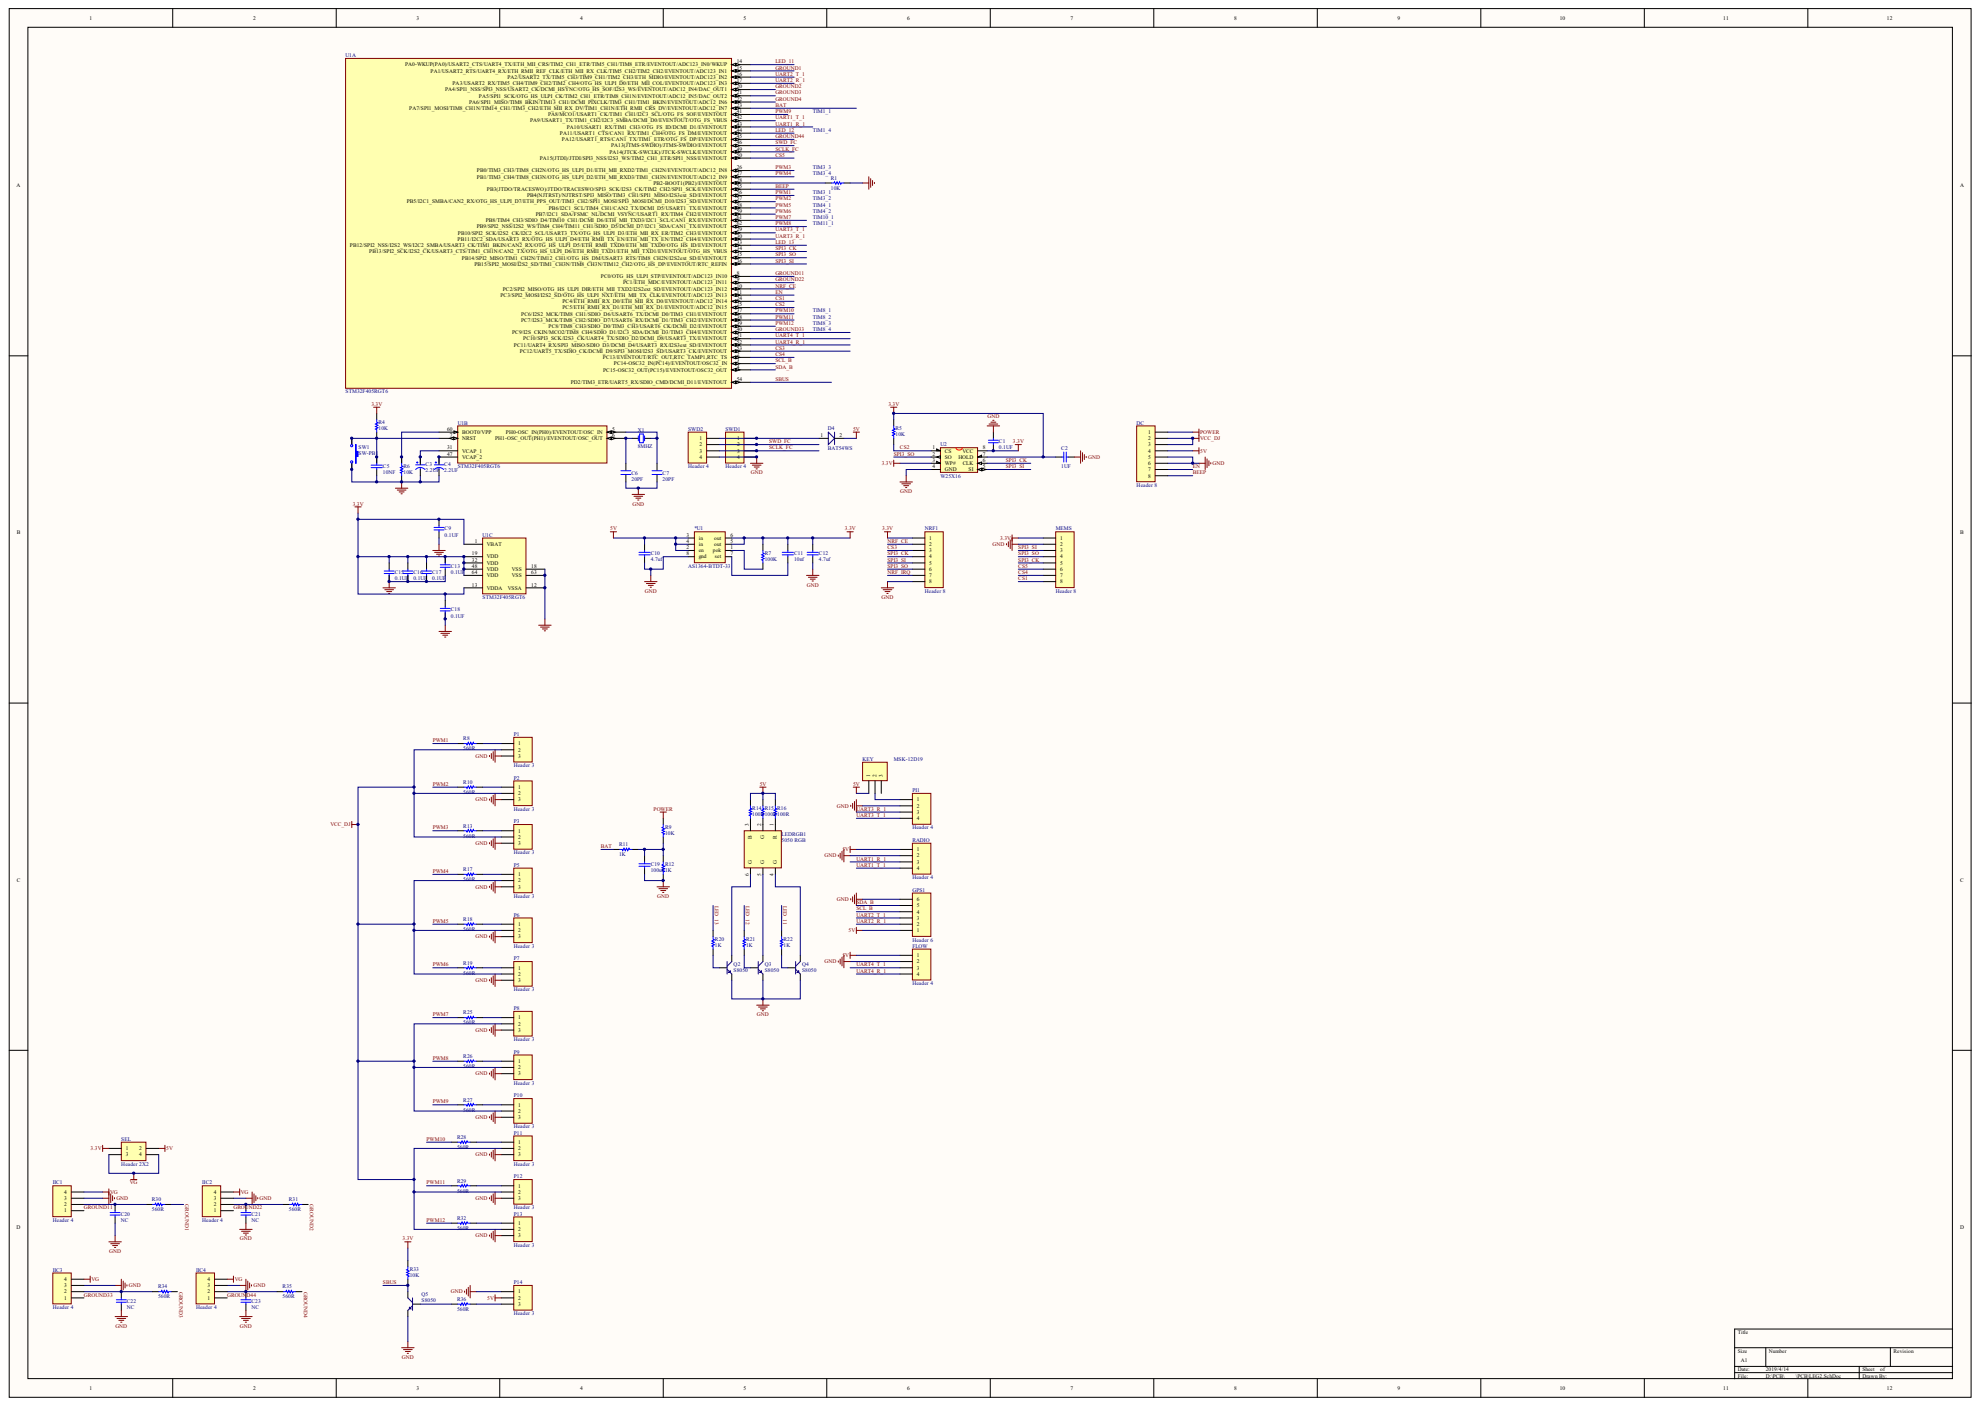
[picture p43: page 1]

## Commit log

2019-03-21 update pcb
    [IMU.xls, 下载器.xls, 供电模块.xls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]
2019-05-15 更新资料和3D打印文件
    [足底带传感器1.STL, 足底带传感器2(需镜像打印).STL]
2019-05-27 更新教程
2019-05-28 压缩程序
2019-05-28 更新使用教程
2019-06-26 更新固件和3D打印文件
    [控制器外壳支撑.STL, 相机支撑可调 2.STL, 相机支撑可调1.STL]
2019-07-07 更新打印机架文件
    [两轴云台1.STL, 两轴云台2.STL, 两轴云台3.STL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]
2019-07-25 更新固件
    [两轴云台2.STL, 两轴云台5.STL]
